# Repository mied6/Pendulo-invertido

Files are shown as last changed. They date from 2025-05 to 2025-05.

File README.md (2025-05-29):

# Práctica 4 - PID en tiempo discreto y Práctica 6 - proyecto péndulo invertido

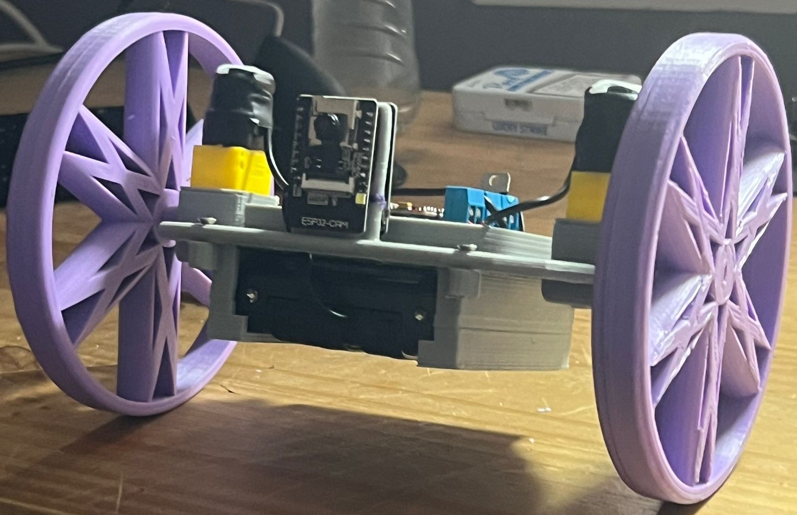
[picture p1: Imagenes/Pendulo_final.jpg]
Péndulo invertido final


### Miguel Estévez Díaz
#### 2º Robótica - Teoría de contol

## Descripción:

Esta práctica combina el diseño de un controlador PID en tiempo discreto (Práctica 4) con su aplicación en un sistema físico real: el control de un péndulo invertido sobre un robot móvil (Práctica 6). El objetivo es lograr el equilibrio vertical del péndulo mediante una estrategia de control implementada en un microcontrolador ESP32.

---

## Metodología:

1. Diseño del hardware necesario -> Diseñar la pcb seleccionando los componentes necesarios para el correcto funcionamiento del pendulo
2. Montage del hardware -> Soldado de los componentes a la pcb.
3. Diseño del cuerpo adecuado -> Pasando por varias versiones tanto del modelo del cuerpo como de las ruedas
4. Diseño de una interfaz web de control y monitoreo del robot -> permitiendo un control "universal" puesto que el servidor va dentro del robot

---

## Objetivos:

1. Estabilidad Perpendicular al Suelo -> Garantizar que el robot sea capaz de mantenerse estable en posición perpendicular al suelo. *Logrado*
2. Compensación de Empujones -> Desarrollar la capacidad del robot para compensar empujones y evitar caídas. *Logrado*
3. Arranque desde Cualquier Posición -> Lograr que el robot pueda iniciar su funcionamiento desde cualquier posición inicial. *Logrado*
4. Implementación de un sistema de control y monitorización web. *Logrado*
5. Interconexión con el módulo de la cámara. *No logrado debido a recibir un módulo defectuoso*

---

## Controlador PID discreto

Para mantener el código limpio, reutilizable y fácil de ampliar, el controlador PID se implementó como una clase externa (`PIDcontrol.h/.cpp`). Esta estructura permite encapsular la lógica de control y utilizar diferentes variantes del algoritmo PID simplemente instanciando distintos objetos.

Se definió una **clase abstracta base `PID`**, de la cual heredan tres implementaciones concretas:

### PID_Discreto

La versión más clásica del PID discreto, basada en la fórmula de diferencias hacia atrás. Calcula el error, acumula la integral y estima la derivada con una simple resta:

```cpp
u[k] = Kp * e[k] + Ki * ∑e[k] + Kd * (e[k] - e[k-1])
```

Se utiliza como base funcional por su sencillez y claridad.

### PID_IIR

Una variante más avanzada que implementa el PID como un **filtro IIR** (respuesta infinita al impulso), utilizando los errores actuales y pasados con coeficientes precalculados (`A0`, `A1`, `A2`).

Esta versión tiene ventajas en estabilidad y respuesta cuando se ajusta correctamente, y es adecuada para sistemas embebidos donde se desea una actualización rápida sin cálculos innecesarios.

### PID_Filtrado

Incorpora una **derivada filtrada mediante un filtro pasabajo**, lo que reduce el ruido en la señal de control, especialmente útil cuando se trabaja con sensores como el MPU6050. Aplica un filtro digital en la parte derivativa del PID, lo que suaviza la salida:

```cpp
D_filtrado[k] = α₁(d₀ + d₁) - α₂ * D_filtrado[k-1]
```

Ideal para escenarios reales con señales ruidosas o derivadas inestables.

---

### Uso en el código principal

Desde el `main.ino`, se puede crear el controlador simplemente así:

```cpp
PID* pid = new PID_Filtrado(Kp, Ki, Kd, dt, N);  // o PID_Discreto o PID_IIR
float control_output = pid->compute(setpoint, measured_angle);
```

Esto permite intercambiar fácilmente el tipo de controlador sin modificar el resto del código del sistema.

---

## Modelos implementados

### Cuerpos:

Para este proyecto se diseñaron 4 versiones del cuerpo diferentes, con las cuales se realizaron diferentes pruevas.

#### Versión 1: 

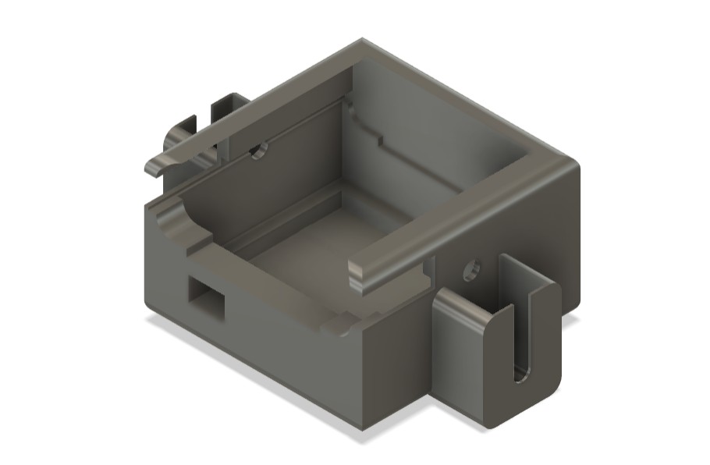
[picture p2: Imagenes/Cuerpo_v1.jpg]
Cuerpo v1


Con esta versión tenía 2 problemas:
1. Las ruedas eran muy pequeñas, permitiendo muy poca inclinación antes de que el cuerpo petara contra el suelo
2. El centro de masas estava muy abajo, y el robot no era capar de compensar bien las caidas 

#### Versión 2: 

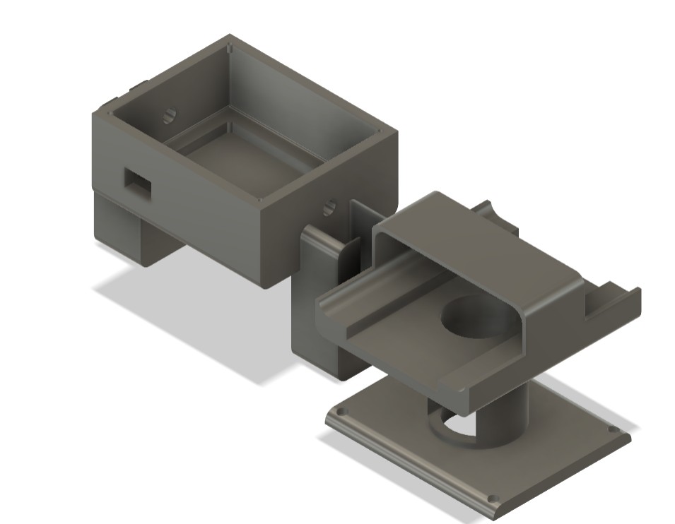
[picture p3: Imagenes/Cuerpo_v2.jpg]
Cuerpo v2


Con esta versión tenía 2 problemas:
1. Los motores son muy poco potentes, con lo cual no alcanzan la suficiente velocidad para compensar la caida
2. esta es más teória, puesto que no pude provar otros motores, el centro de gravedad esta situada 1-2cm demasiado alto.

#### Versión 3: 

Descartando hacer unha versión con el centro de gravedad alto debido a la potencia de los motores pase a diseñar uno con el centro de gravedad bajo.

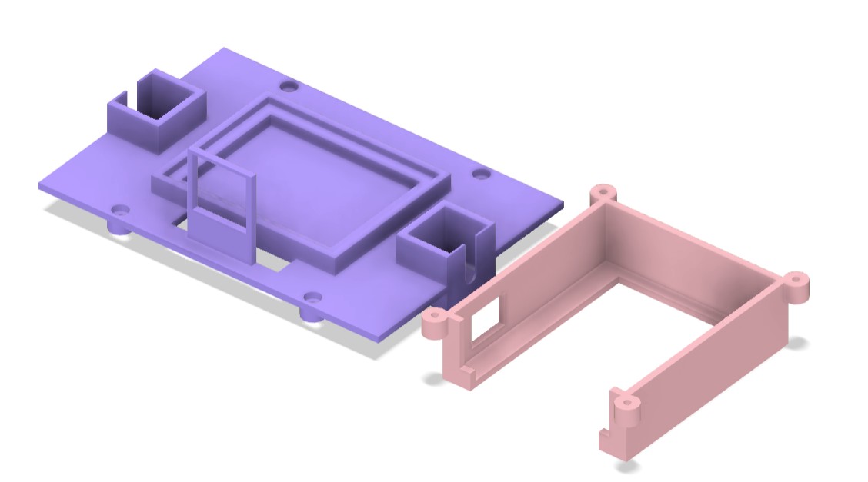
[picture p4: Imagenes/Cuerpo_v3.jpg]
Cuerpo v3


Con esta versión tenía 1 problemas:
1. Las ruedas eran muy pequeñas, permitiendo muy poca inclinación antes de que el cuerpo petara contra el suelo

Cabe recalcar en si que este no fue el motivo por el que la descarte, fue si no porque cuando estava sintonizando el pid dio unha vuelta de golpe partiendo el soporte del modulo de la cámara (el módulo no sufrio ningun golpe, no estava montado en ese momento)

#### Versión 4: 

Visto lo anterior decidí hacer el soporte un poco más ancho, y de paso aproveche para darle un diseño más estético y moderno

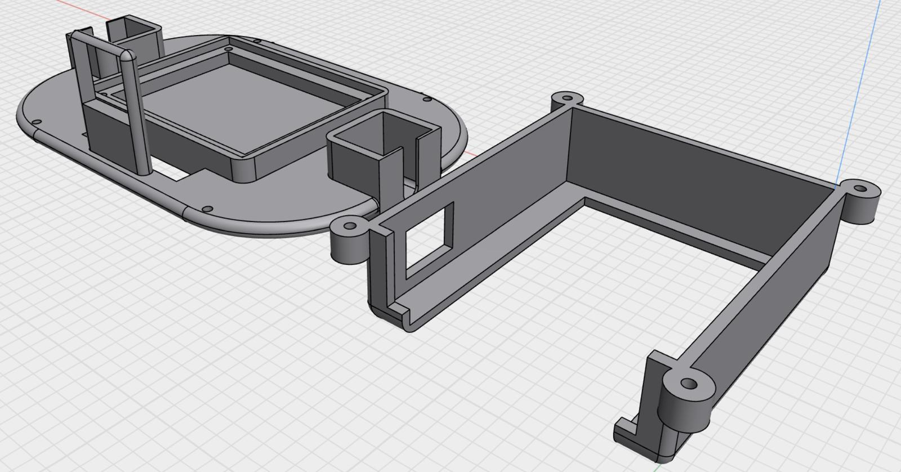
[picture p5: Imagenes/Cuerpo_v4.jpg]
Cuerpo v4


Con esta versión tenía 1 problemas:
1. Las ruedas eran muy pequeñas, permitiendo muy poca inclinación antes de que el cuerpo petara contra el suelo, aunque ya estava solucionado puesto que ya implementara las de la segunda versión, consiguiendo que en caso de que el robot dira una vuelta completa no chocara ni el soporte de la cámara contra el suelo

### Ruedas:

Para este proyecto se diseñaron 3 versiones del cuerpo diferentes, con las cuales se realizaron diferentes pruevas.

#### Versión 1:

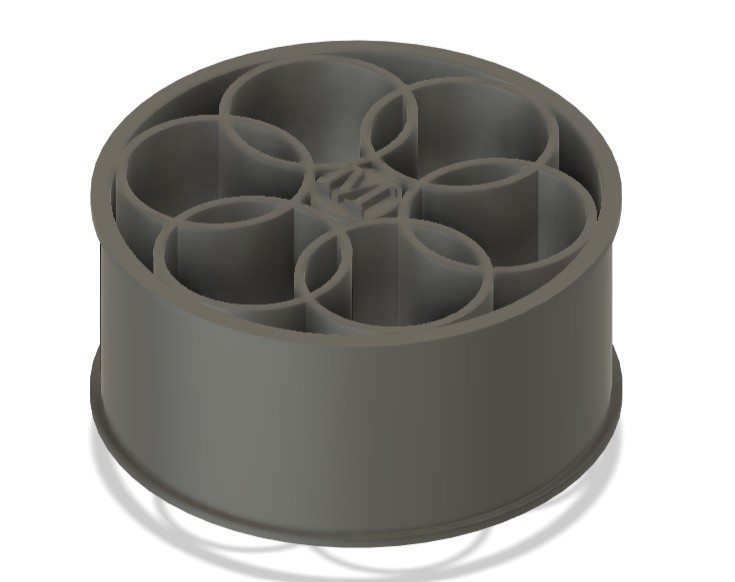
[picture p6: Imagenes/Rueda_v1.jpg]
Rueda v1


Están diseñadas para aprovechar los neumáticos de las ruedas que venían con los motores, es decir un cambio de yantas

En el diseño final no llevan ni al suelo al estar montadas a causa de que la powerbanck es muy ancha (algo más de 2cms)

#### Versión 2: 

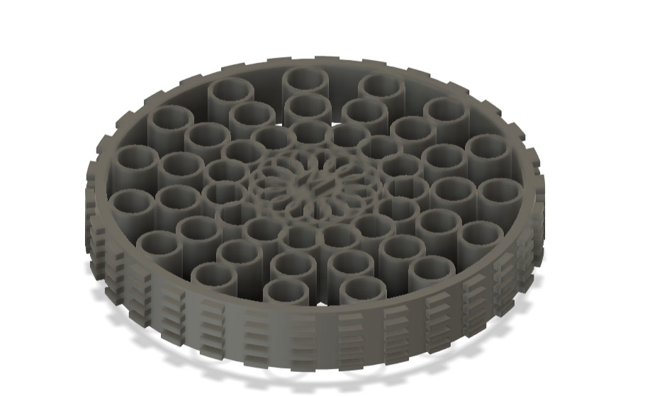
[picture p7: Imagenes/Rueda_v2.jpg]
Rueda v2


Se podría decir que eran las causantes dfe que el cuerpo tuviera poco ángulo de rotación, pero realmente las cambie a causa de la rotura del soporte de la cámara

#### Versión 3: 

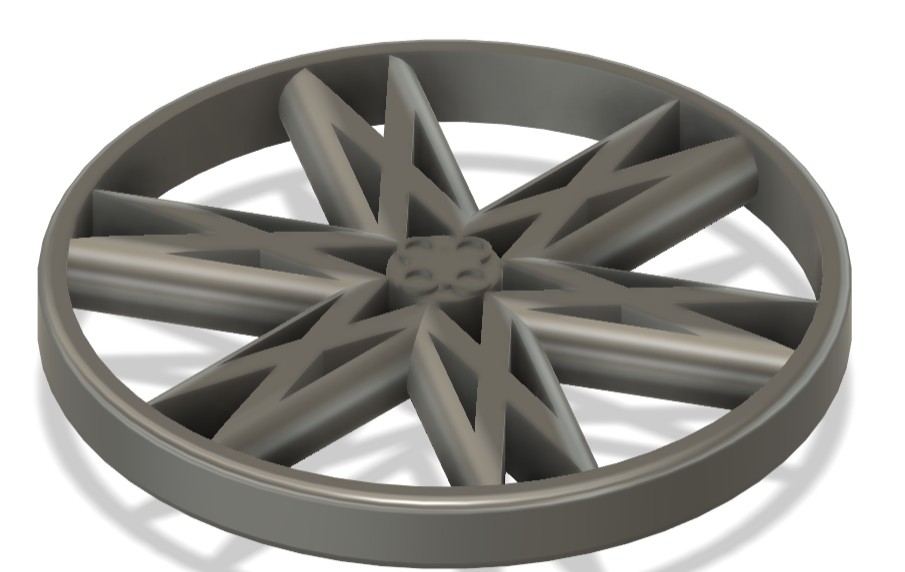
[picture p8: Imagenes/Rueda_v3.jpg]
Rueda v3


Versión definitiva, aunque me huviera gustado hacerla con tacos como la primera versión

---

## Servidor web:

Como en este tipo de implementaciones lo que se busca es desarrollar una interfaz intuytiva y sencilla, con lo cúal me decidí por no poner mucha cosa para usarlo desde un teléfono móvil (la referencia usada fue uno bastante grande, concretamente use de referencia un iphon 13 pro max), obteniendo el siguiente diseño completamente funcional:

<p align="center">
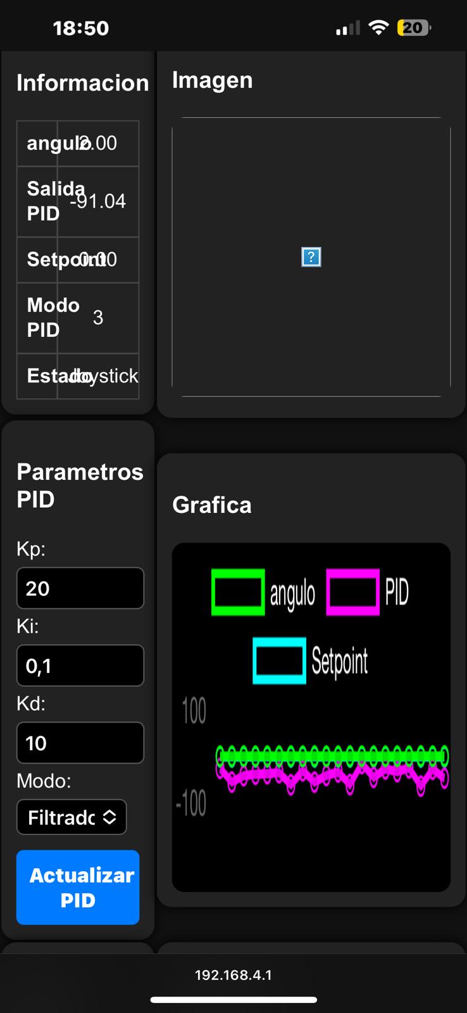
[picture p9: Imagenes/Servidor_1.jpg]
Servidor 1
  
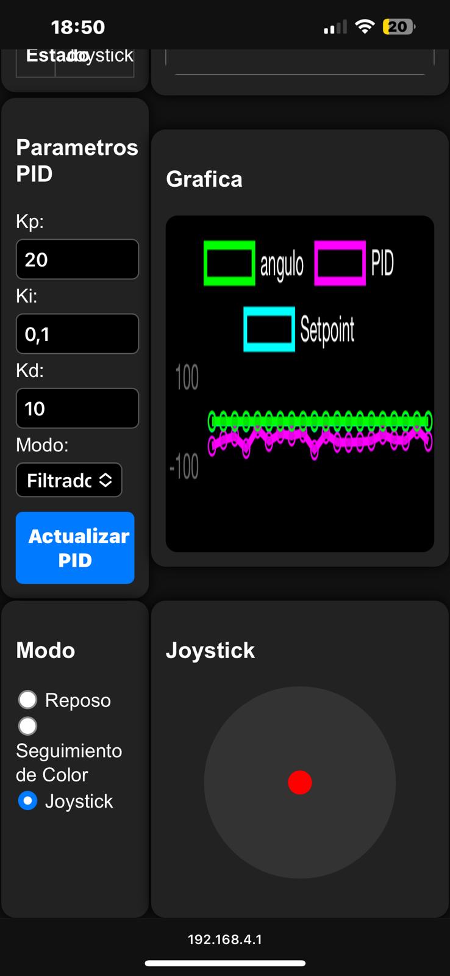
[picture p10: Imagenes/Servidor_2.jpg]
Servidor 2
  
</p>

---

## Conclusiones:

Quitando la parte de añadirle la muestra de la imagen desde la cámara todo funciona perfectamente, autobalanceandose el robot y resistiendo a empujones como se puede ver en en siguiente video: [Ver vídeo de la demo del péndulo](https://youtube.com/shorts/DccQZT0np7g)

Cabe recalcar que a futuro tengo pensado añadirle un sensor de ultrasonidos para permitirle hacer navegaciones en base a el y a la cámara.

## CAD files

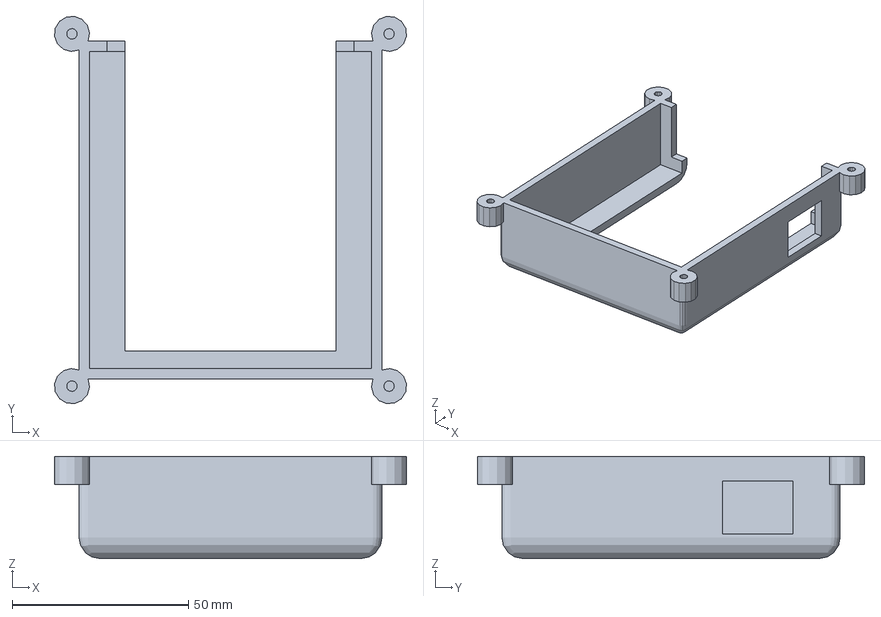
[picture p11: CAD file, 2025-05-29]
Modelos/Pendulo_v4/cuerpo inferior.3mf
99.9 x 109.9 x 29.0 mm

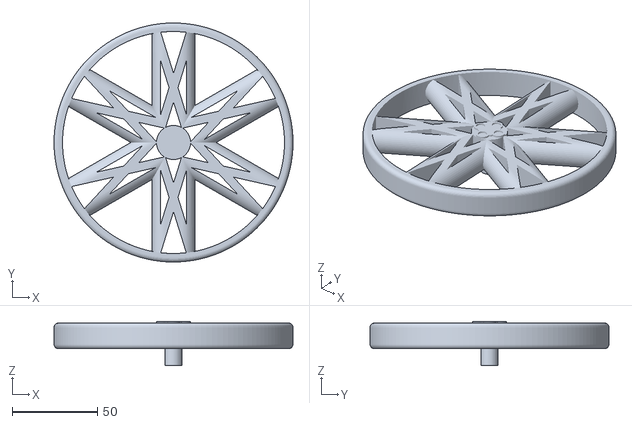
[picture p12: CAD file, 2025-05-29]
Modelos/rueda-v2.stl
140.0 x 140.0 x 26.0

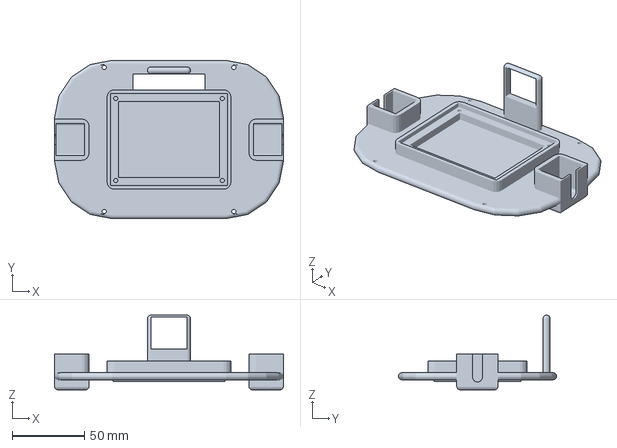
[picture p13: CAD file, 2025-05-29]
Modelos/Pendulo_v4/cuerpo superior.3mf
159.0 x 110.0 x 52.0 mm

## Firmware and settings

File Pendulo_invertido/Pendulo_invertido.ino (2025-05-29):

// Autobalanceador_v6.ino
#include <Wire.h>
#include <MPU6050.h>
#include <WiFi.h>
#include <WebServer.h>
#include <BluetoothSerial.h>
#include "PIDControl.h"

int pid_mode = 3;

MPU6050 mpu;
WebServer server(80);
BluetoothSerial SerialBT;

const int AIN1 = 0, AIN2 = 2, PWMA = 5;
const int BIN1 = 4, BIN2 = 16, PWMB = 17;
const int STBY = 15;

float setpoint = 0.0, measured_value = 0.0, dt = 0.005, output = 0;
float kp = 20.0, ki = 0.1, kd = 10.0;
PID* pid = nullptr;

const char* ssid = "ESP32_Robot";
const char* password = "12345678";

String statusInfo = "";
float desplazamientoX = 0.0, desplazamientoY = 0.0;
bool seguimientoColorActivo = false;
bool controlJoystickActivo = true;

String pageContent() {
  return R"rawliteral(
<!DOCTYPE html><html lang="es"><head>
  <meta name="viewport" content="width=device-width, initial-scale=1.0, user-scalable=no">
  <title>Robot Autobalanceador</title>
  <script src='https://cdn.jsdelivr.net/npm/chart.js'></script>
  <style>
    body { margin: 0; font-family: Arial, sans-serif; background: #111; color: #fff; }
    h1 { text-align: center; padding: 10px 0; font-size: 22px; }
    table { width: 100%; table-layout: fixed; border-spacing: 0; }
    td:first-child { width: 33.33%; }
    td:last-child { width: 66.66%; }

    .box {
      background: #222; padding: 12px; border-radius: 12px;
      box-shadow: 0 0 10px #000; height: 100%; min-height: 240px;
    }
    .status-table {
      width: 100%; border-collapse: collapse;
    }
    .status-table th, .status-table td {
      border: 1px solid #444; padding: 8px; text-align: center;
      font-size: 16px;
    }
    input[type=number], select {
      width: 90%; margin: 4px 0;
      background: #000; color: #fff;
      border: 1px solid #555; border-radius: 6px; padding: 6px;
      font-size: 16px;
    }
    button {
      width: 100%; padding: 10px; font-size: 16px;
      border: none; background: #007aff; color: white;
      border-radius: 6px; font-weight: bold; margin-top: 8px;
    }
    canvas {
      display: block; width: 100% !important;
      height: 280px !important;
      background: #000; border-radius: 10px;
    }

    #joystick {
      width: 160px; height: 160px; margin: auto;
      background: #333; border-radius: 50%;
      position: relative; touch-action: none;
    }
    #dot {
      width: 20px; height: 20px;
      background: red; border-radius: 50%;
      position: absolute; top: 70px; left: 70px;
    }
  </style>
</head><body>
<h1>Robot Autobalanceador</h1>
<table><tr>
  <td><div class="box"><h3>Informacion</h3>
    <table id="status-table" class="status-table">
      <tr><th>Angulo</th><td>-</td></tr>
      <tr><th>Salida PID</th><td>-</td></tr>
      <tr><th>Setpoint</th><td>-</td></tr>
      <tr><th>Modo PID</th><td>-</td></tr>
      <tr><th>Estado</th><td>-</td></tr>
    </table>
  </div></td>
  <td><div class="box"><h3>Imagen</h3>
    <img id="cam" src="http://192.168.4.2/capture" width="100%" style="border-radius: 10px;"/>
  </div></td>
</tr><tr>
  <td><div class="box"><h3>Parametros PID</h3>
    Kp: <input type="number" id="kp" value="20"><br>
    Ki: <input type="number" id="ki" value="0.1"><br>
    Kd: <input type="number" id="kd" value="10"><br>
    Modo: <select id="pidmode">
      <option value="1">Discreto</option>
      <option value="2">IIR</option>
      <option value="3" selected>Filtrado</option>
    </select>
    <button onclick="setPID()">Actualizar PID</button>
  </div></td>
  <td><div class="box"><h3>Grafica</h3>
    <canvas id="chart"></canvas>
  </div></td>
</tr><tr>
  <td><div class="box"><h3>Modo</h3>
    <input type="radio" name="modo" onclick="setModo('reposo')"> Reposo<br>
    <input type="radio" name="modo" onclick="setModo('color')"> Seguimiento de Color<br>
    <input type="radio" name="modo" onclick="setModo('joystick')" checked> Joystick
  </div></td>
  <td><div class="box"><h3>Joystick</h3>
    <div id="joystick"><div id="dot"></div></div>
  </div></td>
</tr></table>

<script>
let angleData=[], pidData=[], setpointData=[], labels=[], maxPoints=20;
const ctx = document.getElementById('chart').getContext('2d');
const chart = new Chart(ctx, {
  type: 'line',
  data: {
    labels: labels,
    datasets: [
      { label: 'angulo', data: angleData, borderColor: 'lime', fill: false },
      { label: 'PID', data: pidData, borderColor: 'magenta', fill: false },
      { label: 'Setpoint', data: setpointData, borderColor: 'cyan', fill: false }
    ]
  },
  options: {
    animation: false,
    scales: { y: { suggestedMin: -90, suggestedMax: 90 } },
    plugins: { legend: { labels: { color: '#fff' } } }
  }
});

function updateChart() {
  fetch('/data').then(r => r.json()).then(d => {
    if (angleData.length >= maxPoints) {
      angleData.shift(); pidData.shift(); setpointData.shift(); labels.shift();
    }
    angleData.push(d.angle);
    pidData.push(d.pid);
    setpointData.push(d.setpoint || 0);
    labels.push('');
    chart.update();
  });
}

function updateStatus() {
  fetch('/status').then(r => r.text()).then(h => {
    document.getElementById('status-table').innerHTML = h;
  });
}

function updateImage() {
  document.getElementById('cam').src = "http://192.168.4.2/capture?ts=" + Date.now();
}

function setPID() {
  const kp = document.getElementById('kp').value;
  const ki = document.getElementById('ki').value;
  const kd = document.getElementById('kd').value;
  const mode = document.getElementById('pidmode').value;
  fetch(`/setPID?kp=${kp}&ki=${ki}&kd=${kd}&mode=${mode}`);
}

function setModo(modo) {
  if (modo === 'color') {
    fetch('/joystick/off'); fetch('/colorTracking/on');
  } else if (modo === 'joystick') {
    fetch('/colorTracking/off'); fetch('/joystick/on');
  } else {
    fetch('/colorTracking/off'); fetch('/joystick/off');
  }
}

const dot = document.getElementById('dot');
const joystick = document.getElementById('joystick');
joystick.addEventListener('pointermove', e => {
  const r = joystick.getBoundingClientRect();
  let x = e.clientX - r.left - r.width / 2;
  let y = e.clientY - r.top - r.height / 2;
  const radius = r.width / 2;
  x = Math.max(-radius, Math.min(radius, x));
  y = Math.max(-radius, Math.min(radius, y));
  dot.style.left = (radius + x - 10) + 'px';
  dot.style.top = (radius + y - 10) + 'px';
  fetch(`/desplazamiento?valueX=${-x}&valueY=${-y}`);
});
['pointerup','pointerleave'].forEach(ev =>
  joystick.addEventListener(ev, () => {
    const radius = joystick.getBoundingClientRect().width / 2;
    dot.style.left = (radius - 10) + 'px';
    dot.style.top = (radius - 10) + 'px';
    fetch('/desplazamiento?valueX=0&valueY=0');
  })
);

setInterval(updateStatus, 500);
setInterval(updateChart, 500);
setInterval(updateImage, 1000);
</script>
</body></html>
)rawliteral";
}

void setup() {
  Serial.begin(115200);
  Wire.begin(); mpu.initialize();
  pinMode(AIN1, OUTPUT); pinMode(AIN2, OUTPUT); pinMode(PWMA, OUTPUT);
  pinMode(BIN1, OUTPUT); pinMode(BIN2, OUTPUT); pinMode(PWMB, OUTPUT);
  pinMode(STBY, OUTPUT); digitalWrite(STBY, HIGH);

  WiFi.softAP(ssid, password);
  delay(300);
  server.begin();
  SerialBT.begin("ESP32_Robot_BT");

  server.on("/", []() { server.send(200, "text/html", pageContent()); });
  server.on("/status", []() { server.send(200, "text/html", statusInfo); });
  server.on("/desplazamiento", []() {
    if (!controlJoystickActivo) return server.send(200, "text/plain", "Joystick desactivado");
    desplazamientoY = server.arg("valueY").toFloat();
    desplazamientoX = -server.arg("valueX").toFloat();
    server.send(200, "text/plain", "Actualizado");
  });
  server.on("/data", []() {
    String json = "{";
    json += "\"angle\":" + String(measured_value, 2) + ",\"pid\":" + String(output, 2);
    json += ",\"setpoint\":" + String(setpoint, 2);
    json += ",\"kp\":" + String(kp, 2) + ",\"ki\":" + String(ki, 2) + ",\"kd\":" + String(kd, 2);
    json += ",\"mode\":" + String(pid_mode);
    json += "}";
    server.send(200, "application/json", json);
  });
  server.on("/setPID", []() {
    kp = server.arg("kp").toFloat(); ki = server.arg("ki").toFloat(); kd = server.arg("kd").toFloat();
    int mode = server.hasArg("mode") ? server.arg("mode").toInt() : 3;
    delete pid;
    pid_mode = mode;
    switch (mode) {
      case 1: pid = new PID_Discreto(kp, ki, kd, dt); break;
      case 2: pid = new PID_IIR(kp, ki, kd, dt); break;
      default: pid = new PID_Filtrado(kp, ki, kd, dt, 5.0); break;
    }
    server.send(200, "text/plain", "PID actualizado");
  });
  server.on("/colorTracking/on", []() {
    seguimientoColorActivo = true;
    controlJoystickActivo = false;
    SerialBT.println("START_COLOR");
    server.send(200, "text/plain", "Seguimiento activado");
  });
  server.on("/colorTracking/off", []() {
    seguimientoColorActivo = false;
    SerialBT.println("STOP_COLOR");
    desplazamientoX = desplazamientoY = 0;
    server.send(200, "text/plain", "Seguimiento desactivado");
  });
  server.on("/joystick/on", []() {
    controlJoystickActivo = true;
    seguimientoColorActivo = false;
    SerialBT.println("STOP_COLOR");
    server.send(200, "text/plain", "Joystick activado");
  });
  server.on("/joystick/off", []() {
    controlJoystickActivo = false;
    server.send(200, "text/plain", "Joystick desactivado");
  });

  pid = new PID_Filtrado(kp, ki, kd, dt, 5.0);
}

void applyMotorA(float pwm) {
  pwm = constrain(pwm, -255, 255);
  digitalWrite(AIN1, pwm > 0 ? LOW : HIGH);
  digitalWrite(AIN2, pwm > 0 ? HIGH : LOW);
  analogWrite(PWMA, abs(pwm));
}

void applyMotorB(float pwm) {
  pwm = constrain(-pwm, -255, 255);
  digitalWrite(BIN1, pwm > 0 ? LOW : HIGH);
  digitalWrite(BIN2, pwm > 0 ? HIGH : LOW);
  analogWrite(PWMB, abs(pwm));
}

void applyMotors(float pwm1, float pwm2) {
  applyMotorA(pwm1);
  applyMotorB(pwm2);
}

float getAngle() {
  int16_t ax, ay, az; mpu.getAcceleration(&ax, &ay, &az);
  return atan2(ay, az) * 180 / PI;
}

void loop() {
  static unsigned long lastControl = 0, lastServer = 0;
  unsigned long now = micros();
  if (now - lastControl >= dt * 1e6) {
    lastControl = now;
    measured_value = getAngle();
    
    // Solo ajustamos el setpoint con el joystick
    if (controlJoystickActivo) {    } else if (!seguimientoColorActivo) {
      setpoint = 0.0;  // Reposo
    }

    output = pid->compute(setpoint, measured_value);
    output = constrain(output, -255, 255);

    if (seguimientoColorActivo && SerialBT.available()) {
      String datos = SerialBT.readStringUntil('\n');
      int sep = datos.indexOf(',');
      if (sep > 0) {
        float x = datos.substring(0, sep).toFloat();
        float y = datos.substring(sep + 1).toFloat();
        desplazamientoX = (x - 160) / 1.6;
        desplazamientoY = -(y - 120) / 10;
      }
    }

    float pwmAvance = desplazamientoY * 1.75;
    float pwmGiro = - desplazamientoX * 1.75;
    applyMotors(output + pwmAvance - pwmGiro, output + pwmAvance + pwmGiro);
  }

  server.handleClient();

  if (millis() - lastServer > 10) {
    lastServer = millis();
    statusInfo = "<tr><th>angulo</th><td>" + String(measured_value, 2) + "</td></tr>";
    statusInfo += "<tr><th>Salida PID</th><td>" + String(output, 2) + "</td></tr>";
    statusInfo += "<tr><th>Setpoint</th><td>" + String(setpoint, 2) + "</td></tr>";
    statusInfo += "<tr><th>Modo PID</th><td>" + String(pid_mode) + "</td></tr>";
    statusInfo += "<tr><th>Estado</th><td>";
    statusInfo += seguimientoColorActivo ? "Color" : (controlJoystickActivo ? "Joystick" : "Reposo");
    statusInfo += "</td></tr>";
  }
}

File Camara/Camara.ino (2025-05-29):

#include "esp_camera.h"
#include <WiFi.h>

// === PINOUT PARA AI-Thinker ESP32-CAM ===
#define PWDN_GPIO_NUM    -1
#define RESET_GPIO_NUM   -1
#define XCLK_GPIO_NUM     0
#define SIOD_GPIO_NUM    26
#define SIOC_GPIO_NUM    27
#define Y9_GPIO_NUM      35
#define Y8_GPIO_NUM      34
#define Y7_GPIO_NUM      39
#define Y6_GPIO_NUM      36
#define Y5_GPIO_NUM      21
#define Y4_GPIO_NUM      19
#define Y3_GPIO_NUM      18
#define Y2_GPIO_NUM       5
#define VSYNC_GPIO_NUM   25
#define HREF_GPIO_NUM    23
#define PCLK_GPIO_NUM    22

// === Credenciales WiFi (modo AP) ===
const char* ssid = "ESP32_Robot";
const char* password = "12345678";

// IP fija
IPAddress local_IP(192, 168, 4, 2);
IPAddress gateway(192, 168, 4, 1);
IPAddress subnet(255, 255, 255, 0);

WiFiServer server(80);

void startCamera() {
  camera_config_t config;
  config.ledc_channel = LEDC_CHANNEL_0;
  config.ledc_timer   = LEDC_TIMER_0;
  config.pin_d0       = Y2_GPIO_NUM;
  config.pin_d1       = Y3_GPIO_NUM;
  config.pin_d2       = Y4_GPIO_NUM;
  config.pin_d3       = Y5_GPIO_NUM;
  config.pin_d4       = Y6_GPIO_NUM;
  config.pin_d5       = Y7_GPIO_NUM;
  config.pin_d6       = Y8_GPIO_NUM;
  config.pin_d7       = Y9_GPIO_NUM;
  config.pin_xclk     = XCLK_GPIO_NUM;
  config.pin_pclk     = PCLK_GPIO_NUM;
  config.pin_vsync    = VSYNC_GPIO_NUM;
  config.pin_href     = HREF_GPIO_NUM;
  config.pin_sscb_sda = SIOD_GPIO_NUM;
  config.pin_sscb_scl = SIOC_GPIO_NUM;
  config.pin_pwdn     = PWDN_GPIO_NUM;
  config.pin_reset    = RESET_GPIO_NUM;
  config.xclk_freq_hz = 20000000;
  config.pixel_format = PIXFORMAT_JPEG;

  config.frame_size    = FRAMESIZE_QVGA;  // 320x240
  config.jpeg_quality  = 12;
  config.fb_count      = 1;

  // Inicializar cámara
  esp_err_t err = esp_camera_init(&config);
  if (err != ESP_OK) {
    Serial.printf("Error al iniciar la cámara: 0x%x\n", err);
    return;
  }
}

void setup() {
  Serial.begin(115200);

  WiFi.softAP(ssid, password);
  delay(500);
  WiFi.softAPConfig(local_IP, gateway, subnet);

  Serial.println("Red WiFi creada.");
  Serial.print("IP local: ");
  Serial.println(WiFi.softAPIP());

  startCamera();
  server.begin();
}

void loop() {
  WiFiClient client = server.available();
  if (!client) return;

  while (!client.available()) delay(1);
  String request = client.readStringUntil('\r');
  client.readStringUntil('\n');

  if (request.indexOf("/capture") != -1) {
    camera_fb_t* fb = esp_camera_fb_get();
    if (!fb) {
      Serial.println("Error capturando imagen");
      client.println("HTTP/1.1 500 Internal Server Error");
      return;
    }

    client.println("HTTP/1.1 200 OK");
    client.println("Content-Type: image/jpeg");
    client.println("Content-Length: " + String(fb->len));
    client.println("Connection: close");
    client.println();
    client.write(fb->buf, fb->len);
    esp_camera_fb_return(fb);
  } else {
    client.println("HTTP/1.1 404 Not Found");
    client.println("Connection: close");
    client.println();
  }
}
